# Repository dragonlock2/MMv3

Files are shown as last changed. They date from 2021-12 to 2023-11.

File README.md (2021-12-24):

# MMv3

MMv3 is the 3rd generation robot platform used to teach the IEEE Micromouse DeCal at UC Berkeley. It was designed with usability, manufacturability, size, and cost in mind.

## Setup

1. Follow the assembly instructions in [lab1](docs/lab1.md) using the latest **BOM** (see releases).
2. Plug mouse into your computer and upload the latest **firmware.uf2** (see releases) by dragging the file into the `RPI-RP2` folder that shows up. It should disappear and reappear as a `CIRCUITPY` folder.
    * If you've uploaded firmware before, you'll need to hold the `BOOTSEL` button on the Pi Pico while plugging in.
3. Download the latest CircuitPython [libraries](https://circuitpython.org/libraries) (for Version 7.x) and upload the following ones to the lib/ folder on your mouse.
    * adafruit_motor/
    * adafruit_onewire/
    * neopixel.mpy

## Labs

Skeleton lab code, lab documents, and solutions are stored in [labs/](labs/), [docs/](docs/), and [solutions/](solutions/), respectively. To get started with a lab, simply copy the contents of the folder over to the CircuitPython drive and edit files from there.

* [sanity](docs/sanity.md) - Hardware Check
* [lab1](docs/lab1.md) - Assembly and CircuitPython Basics
* [lab2](docs/lab2.md) - Encoders
* [lab3](docs/lab3.md) - IR Sensors
* [lab4](docs/lab4.md) - Odometry and Motor Control
* [lab5](docs/lab5.md) - Intro to PID
* [lab6](docs/lab6.md) - More PID
* [lab7](docs/lab7.md) - Maze Solving Primitives **(WIP)**
* lab8 - Flood Fill **(WIP)**

## Compiling CircuitPython

The DS28E05 1-Wire EEPROM operates at overdrive speeds only. Adding support involves compiling a patched version of CircuitPython.

1. Follow these [instructions](https://learn.adafruit.com/building-circuitpython/introduction) to get your system set up for compilation.
2. Follow these [instructions](https://learn.adafruit.com/building-circuitpython/build-circuitpython) to clone CircuitPython and do further setup but don't compile CircuitPython just yet.
3. Apply [circuitpython.patch](circuitpython.patch) using `patch -p1 < circuitpython.patch`
    * Also apply [macos.patch](macos.patch) if using MacOS.
4. Compile CircuitPython with `cd ports/raspberrypi && make  BOARD=raspberry_pi_pico`
5. Upload the resulting firmware.uf2!

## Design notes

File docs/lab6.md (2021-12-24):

# Lab 6: More PID

## Background

In the previous lab we were able to get our mice driving a certain distance reasonably straight with just proportional control. This week, we'll learn how to correct for persistent steady state error, turn in place, and follow walls.

Recall our implementation of a **proportional (P) controller** from the last lab.

<p align="center">
    
</p>

Proportional control works pretty well for making our mouse drive straight, but you may have noticed a constant offset error. The motors naturally travel at different speeds given the same power and the constant offset error actually accounts for that difference. If we had zero error, we'd actually apply the same power to each motor, generating an error. How might we fix this? What if we kept track of the total error?

<p align="center">
    
</p>

This is called a **proportional-integral (PI) controller**. The integral keeps track of the total error (both positive and negative) since we first started the controller. Even small errors will cause the integral term to eventually grow large enough and get  to push our mouse back on track.

In order to dampen oscillations and prevent overshoot, we might want to consider the derivative of our error too. This prevents our error from changing too quickly.

<p align="center">
    
</p>

With these three terms, we have our **proportional-integral-derivative (PID) controller**. , , and  are tunable gains that determine the behavior of our error (rise time, peak, overshoot, etc.).

Let's go over what each of the terms in PID means.

* The **P** term (**proportional**) increases our correction proportionally to the error: the higher our error, the more power we should apply to correct for it.
* The **I** term (**integral**) compensates for long-term error and drift by integrating the error over time. While a small tendency for our mouse to veer to the right might have little effect on the P term, it’ll cause the I term to build up until the system reaches the setpoint perfectly.
* The **D** term (**derivative**) takes the derivative of the error with respect to time. Systems often have inertia: the faster our error is already decreasing, the less power we need to apply to correct for it. This dampens our controller and reduces overshooting.

Note this checkpoint has no code.

### Checkoff #1

1. We only have individual measurements of error, not a continuous function. How might we estimate the integral of the error?
2. How might we estimate the derivative of the error?
3. One potential issue with PID control is **integral windup**. You can read about it [here](https://en.wikipedia.org/wiki/Integral_windup). What are some ways of preventing integral windup?

## Turning

Copy over the skeleton code in [labs/lab6/](../labs/lab6) onto your mouse. To encourage code readability, we've added a couple of function definitions that modularize the controller. Adapt your P controller code from [Lab 5](lab5.md) to these functions by filling out the TODOs. If you have a better way of organizing the functions, feel free to change things. Ultimately, it should have the same behavior as Checkoff #2 from Lab 5.

Next, add I and D terms to both your angular and linear P controllers. You may find the `global` or `nonlocal` keywords to be useful for accessing variables defined outside of a function. We highly recommend just tuning the PID constants for your linear controller first and then tuning the angular controller when you implement turning. It's generally easier when that specific controller is being exercised. Good starting values are 10x smaller than .

Finally, have your mouse turn 90° in place. This should be as simple as setting a different target . For an added challenge, let's create a `turn_left` function which internally loops until the mouse turns about 90° (you choose the threshold for acceptable error) before returning. You may find it useful to be able to reset the odometry back to 0 with the following function.

```python
def reset_odometry():
    lenc.position, renc.position = 0, 0
```

### Checkoff #2

1. Demonstrate your working PID loop driving straight a set distance.
2. Demonstrate your working PID loop turning in place by 90°.
3. Demonstrate turning in place by 90° and then stopping for one second before turning another 90° and so on.
4. Explain your implementation of your integral term. Did you account for integral windup?

## Wall Following

When we're driving in a maze, our mouse will always be slightly misaligned with reference to a wall. Despite driving perfectly straight, this slight error will eventually cause us to crash. By performing feedback control with our IR sensors, we can correct for any misalignment!

In the interest of developing maze solving primitives in the future, you will implement a `forward()` function that will have the mouse drive forwards 180mm and stop. While driving forward, maintain a fixed 45mm distance from a wall on the left.

Optimally, stable wall following means maintaining a 0° angle with respect to the wall. With just one sensor, it's impossible to determine the angle because multiple angles can correspond to the same sensed distance. Performing feedback control on just that sensor works, but it relies on the mouse moving a bit to correct for angular errors. With two sensors, we can determine the angle from the wall based on the difference between the sensors. Wall following could then be implemented as just setting the angle of the mouse based on the distance error and letting its forward motion correct for the distance error.

To implement wall following, start by taking your distance measurement code from lab 3 and your linear and angular PID controllers from the previous checkoff. Conceptually, we want to change the definitions of `theta` and `theta_target` for the angular controller. Based on what was discussed previously, what are the new definitions of `theta` and `theta_target`?

Don't worry about implementing a PID controller for this as a P controller is adequate. Tuning can be a bit tricky. We've found that `Kp_theta=0.01` and `Kp_ang=0.01` work pretty well. Our reference solution uses `Kp_theta` to scale the distance error to set `theta_target`. Since we assume the mouse drives pretty straight and isn't very misaligned, don't worry about tuning your controller to work well for large errors.

### Checkoff #3

1. Demonstrate your wall following code by calling `forward()` once every second.
2. How might you extend your code to drive straight in between two walls?

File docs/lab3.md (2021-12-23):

# Lab 3: IR Sensors

## Background

IR sensors work by sending out IR light and measuring the amount reflected back. They take a lot more work to calibrate and are surface dependent, but are far cheaper and faster than the ToF sensors we used to use. Our mouse has 6 of these sensors split into 3 pairs (center/front, left, right). Having 2 sensors per side allows us to statically determine both the distance and angle of the nearest surface.

IR sensors consist of both an IR emitter and detector. IR emitters draw around 50mA each when on, so we have a switch to turn them off when not needed. IR detectors shift their IV curve based on light intensity like in the following graph.

<p align="center">
    
</p>

To convert that to a readable voltage signal, we'll use a setup similar to a resistor divider. It's noisier and less tunable compared to a transimpedance amplifier, but uses only one resistor. By placing the IR detector in reverse bias, we use the flatter region of the IV curve. Since the current varies linearly with light intensity, the voltage also varies linearly. MMv3 uses the following circuit (pull-up resistor not shown).

<p align="center">
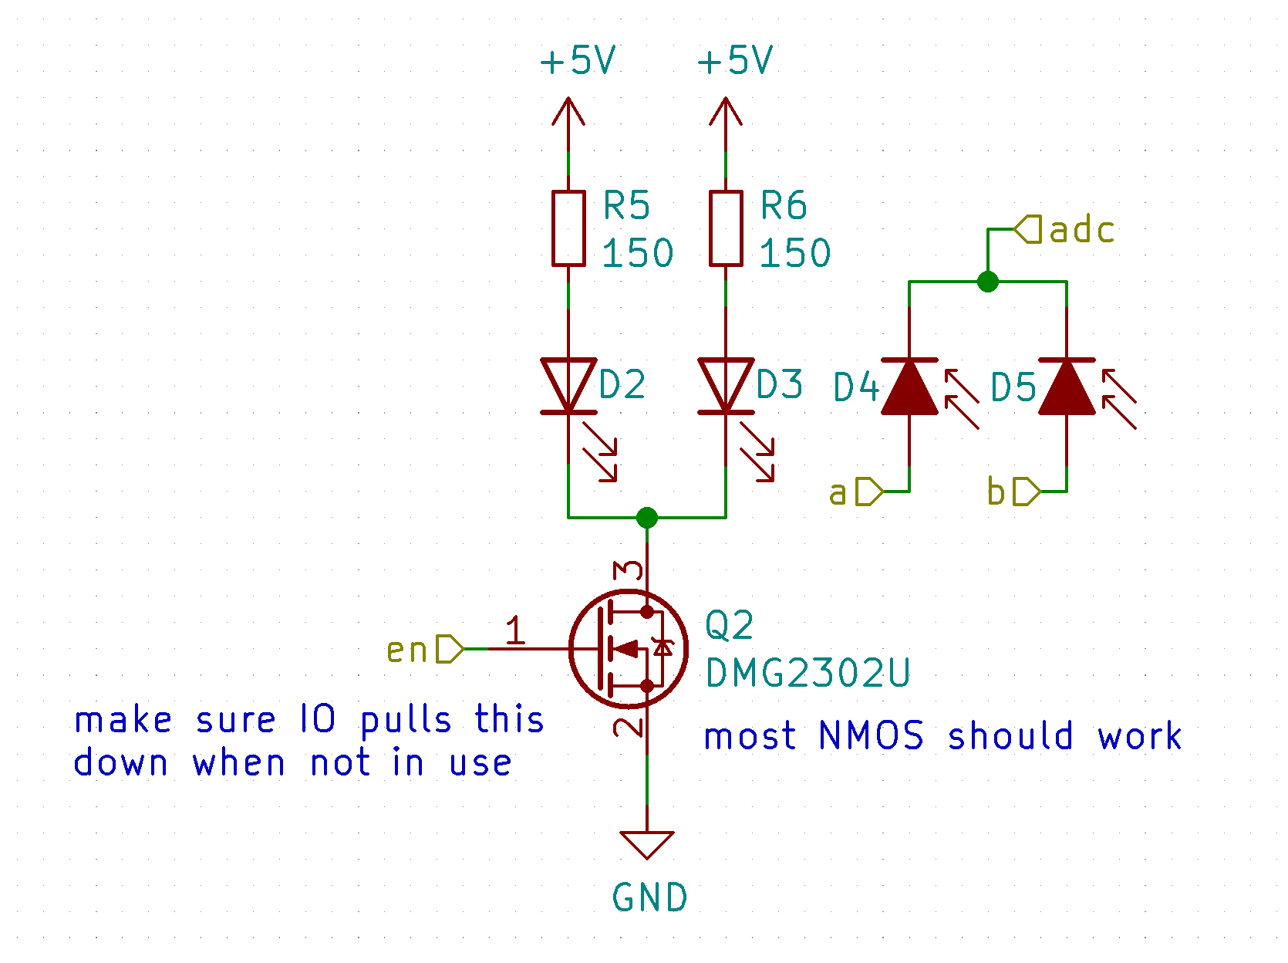
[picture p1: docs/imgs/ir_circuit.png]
    
</p>

## Read One Sensor

Since we have 6 total analog sensors but only 3 ADC pins on the Pi Pico, we need to multiplex 2 sensors onto each pin. We use one extra pin on each IR detector in open-drain mode to fully disconnect or connect it to ground. To read in one sensor, we perform the following steps.

1. Enable the IR emitters (set pin to `True`).
2. Enable the chosen sensor by connecting it to ground (set pin to `False`).
3. Wait around 1ms for things to settle.
4. Take the reading.
5. Disable the chosen sensor by setting the pin to open-drain (set pin to `True`).
6. Disable the IR emitters (set pin to `False`).

Baesd on the above steps and the `AnalogIn` [documentation](https://circuitpython.readthedocs.io/en/latest/shared-bindings/analogio/index.html), fill out the below TODOs to print out readings from the left IR sensor pair (`lir_a` and `lir_b`).

```python
import board
import time
import digitalio
from analogio import AnalogIn

l_en  = """TODO create DigitalInOut output on GP7"""
l_adc = """TODO create AnalogIn on GP28"""

l_a   = digitalio.DigitalInOut(board.GP5)
l_a.direction  = digitalio.Direction.OUTPUT
l_a.drive_mode = digitalio.DriveMode.OPEN_DRAIN
l_a.value = True # high Z mode

l_b = """TODO create DigitalInOut on GP6 in open-drain mode"""

while True:
    # TODO enable IR emitters using l_en
    # TODO enable chosen sensor l_a or l_b
    # TODO wait a bit
    # TODO take analog reading for future printing
    # TODO disable chosen sensor l_a or l_b
    # TODO disable IR emitters using l_en
    time.sleep(0.05)
```

### Checkoff #1

1. Demonstrate one working sensor.

## Read All the Sensors

In order to simplify the whole process of multiplexing and reading from multiple sensors, we wrote a library. Upload `irsensor.py` from [sanity/](../labs/sanity) to serve as the library. Read through `irsensor.py` to instantiate and use it and fill out the below TODOs to print out all sensor readings in real time.

```python
import board
import time

from irsensor import IRSensors

ir = IRSensors(
    """TODO sensor | en   | a    | b    | adc"""
    """TODO lir    | GP7  | GP5  | GP6  | GP28"""
    """TODO cir    | GP9  | GP10 | GP11 | GP26"""
    """TODO rir    | GP21 | GP20 | GP22 | GP27"""
)

while True:
    """TODO get and print all sensor readings"""
    time.sleep(0.05)
```

### Checkoff #2

1. Demonstrate all of your working sensors.

## Calibration

Let's try estimating actual distances from the sensor values. Empirically, the relationship is linear below around 60mm and rises sharply beyond that due to the angled sensors seeing above the wall. Based on maze cell size, we really only need accurate distances around 50mm for wall following and just binary wall detection beyond that.

<p align="center">
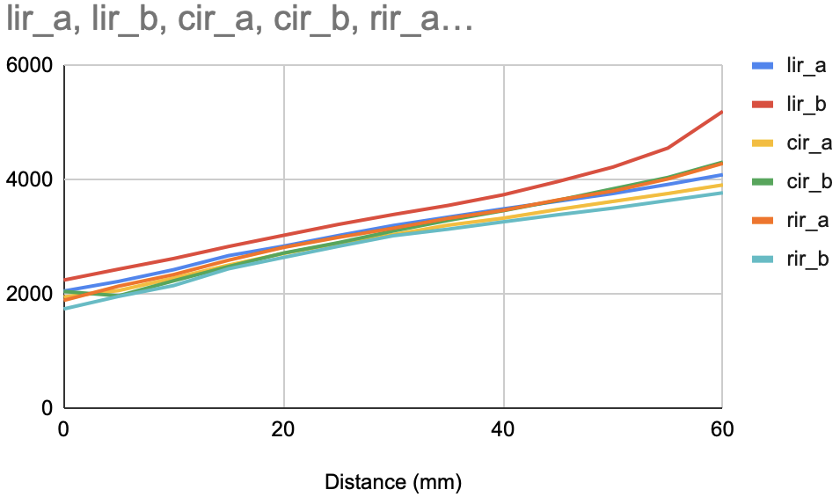
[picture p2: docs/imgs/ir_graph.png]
    
    <br>
    <a><b>IR Sensor Linear Region</b></a>
</p>

Load up [`code.py`](../labs/lab3/code.py) which contains code to automate finding the constants. You'll be using a maze wall and ruler to take readings at various distances. The code then uses least squares to fit a line to the points and prints out the constants at the end. The equation using these constants to convert sensor readings to distances can be expressed as follows.

<p align="center">
    
</p>

### Checkoff #3

1. Run the calibration code and save the constants somewhere.
2. Using the constants, write code to convert sensor values to distances.

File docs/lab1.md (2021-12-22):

# Lab 1: Assembly and CircuitPython Basics

## Assembly

Download the `ibom.html` from the [release](https://github.com/dragonlock2/MMv3/releases) that matches your board revision and open it in your preferred browser. The interactive BOM (bill of materials) shows what parts are needed on your mouse's PCB (printed circuit board) and where they need to be placed.

Also check the latest release for any manufacturing notes to make an older board functionally equivalent to the newest revision.

### Reflow Soldering

Let's start with the back of the PCB which is where the majority of parts are located. Click `B` in the top right to show just the back.

<p align="center">
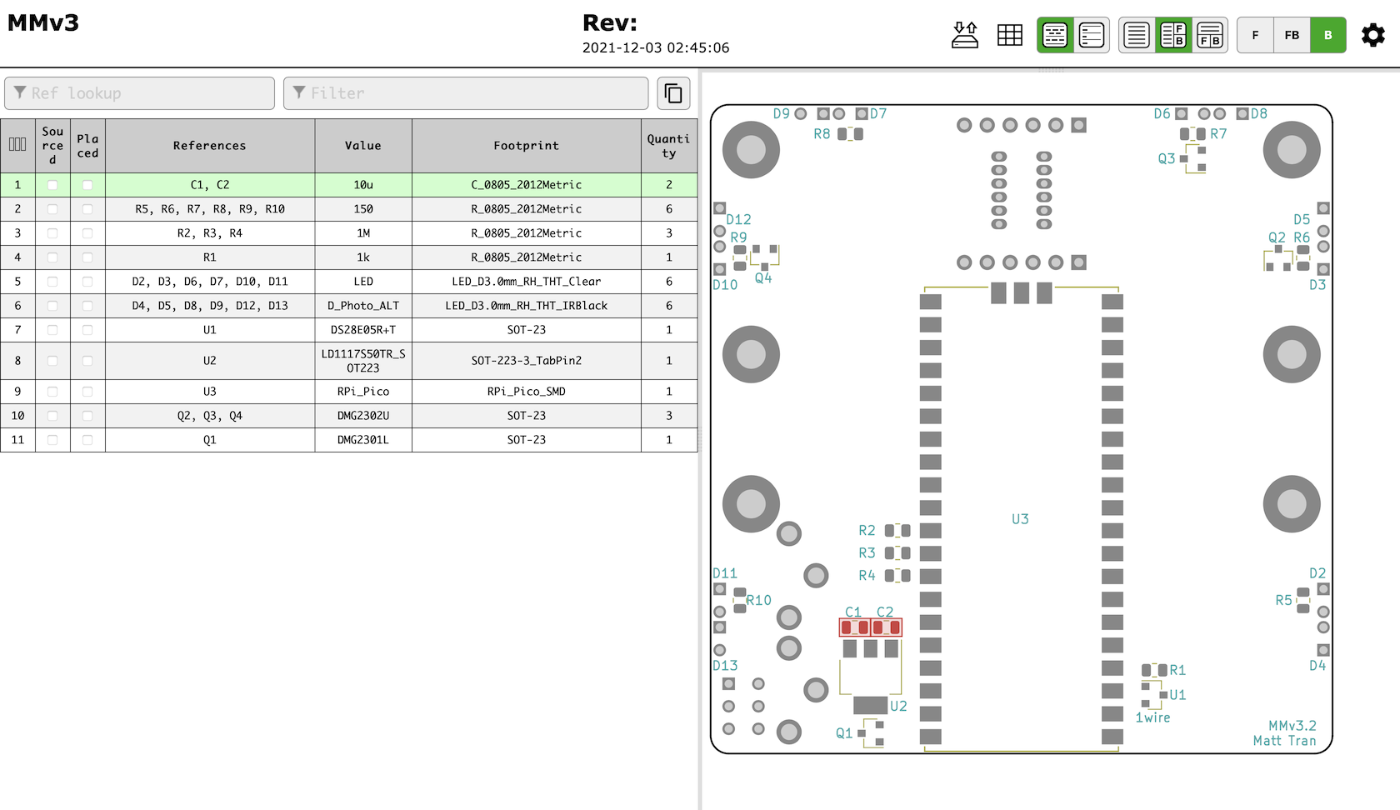
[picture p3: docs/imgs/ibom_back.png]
    
    <br>
    <a><b>iBOM Back</b></a>
</p>

Rather than solder each part by hand, we'll use reflow soldering which does it all at once. In reflow soldering, we place components on top of pads covered in solder paste before sending the whole thing through an oven to melt the solder, making permanent joints.

<p align="center">
    
    <br>
    <a><b>Reflow Solder Process</b></a>
</p>

Let's start by applying the solder paste using a **solder stencil**. Instead of squeezing the perfect amount onto each pad by hand, we can do it all at once by spreading paste over a stencil with holes cut out precisely where we want paste. For a good solder paste application, it's important to make sure the stencil is flush against the PCB and stays aligned. The process is very forgiving, so don't worry if your paste looks messy or goes a bit outside the pads.

<p align="center">
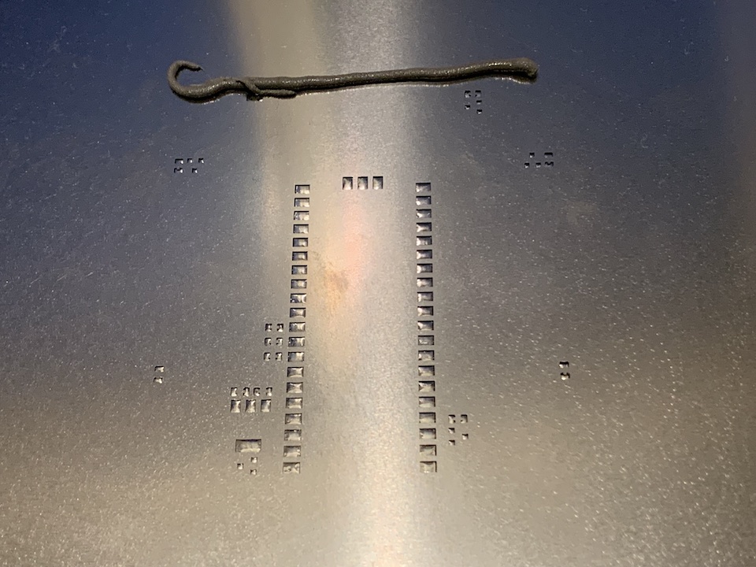
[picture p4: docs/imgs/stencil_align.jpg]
    
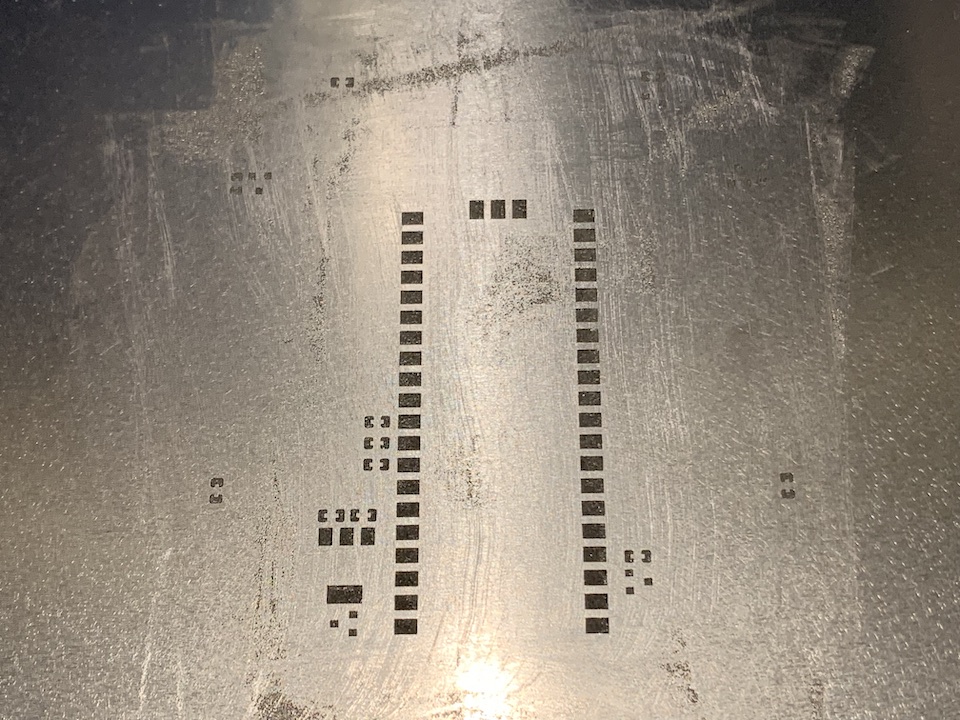
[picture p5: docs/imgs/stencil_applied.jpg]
    
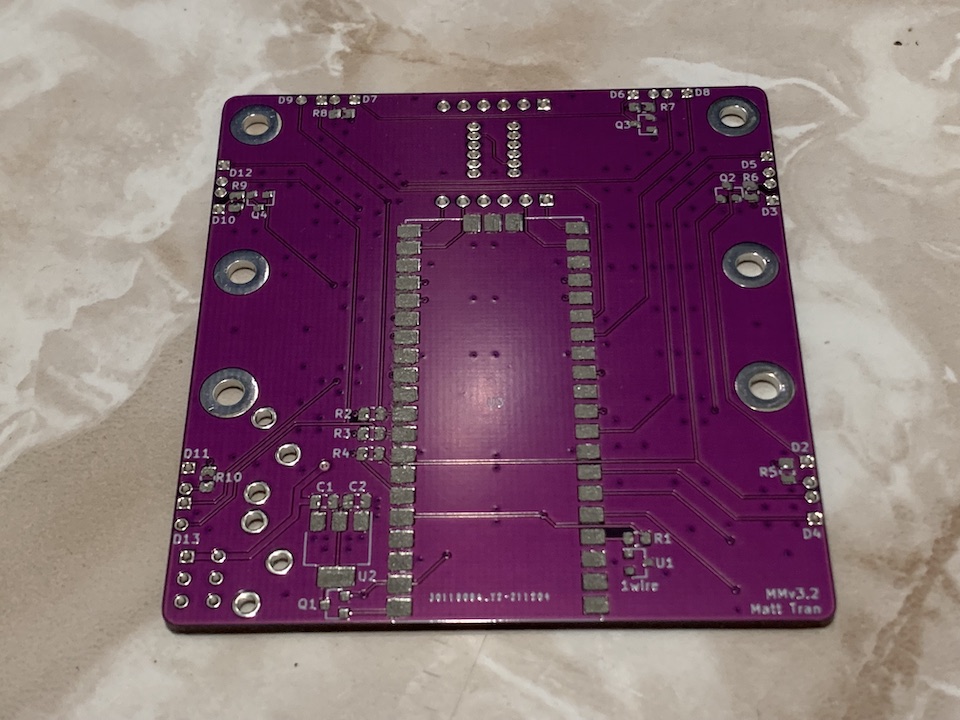
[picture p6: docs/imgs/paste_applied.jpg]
    
    <br>
    <a><b>Solder Paste Application Process</b></a>
</p>

Now it's time for component placement. Following the `ibom.html`, place all of the components for the back side. None of the symmetric components have polarity, so don't worry about part orientation. Tweezers will be very useful, but don't squeeze too hard or your component will go flying. When placing components, press down gently so that it digs into the paste a bit to prevent it from moving. Again, the process is quite forgiving so don't worry if your parts aren't perfectly aligned as solder surface tension will generally pull them into alignment.

<p align="center">
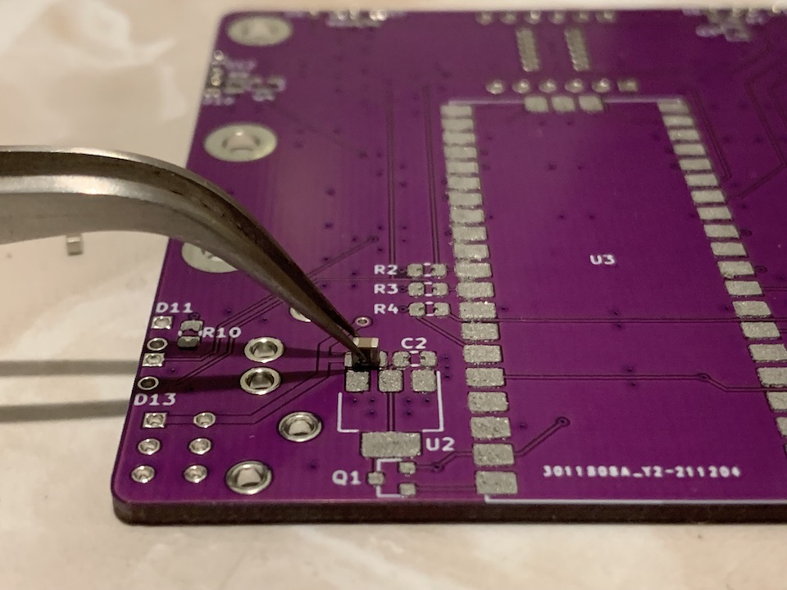
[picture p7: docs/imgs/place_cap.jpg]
    
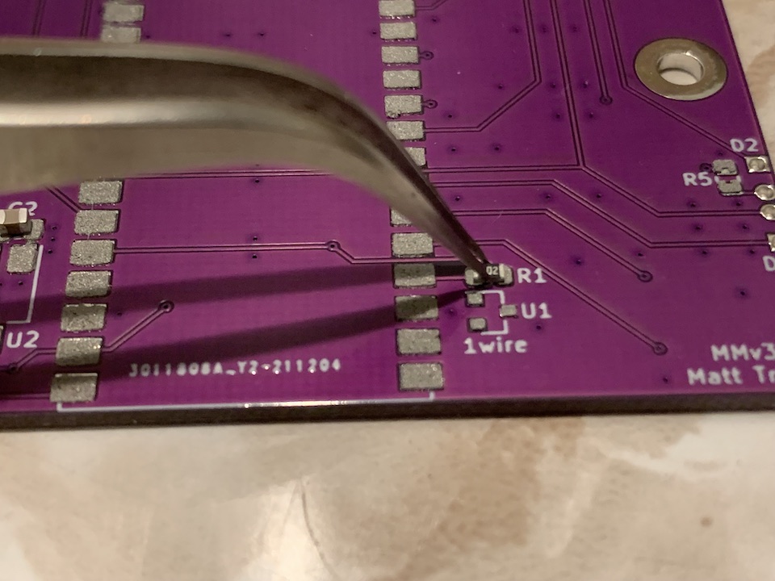
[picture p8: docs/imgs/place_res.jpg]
    
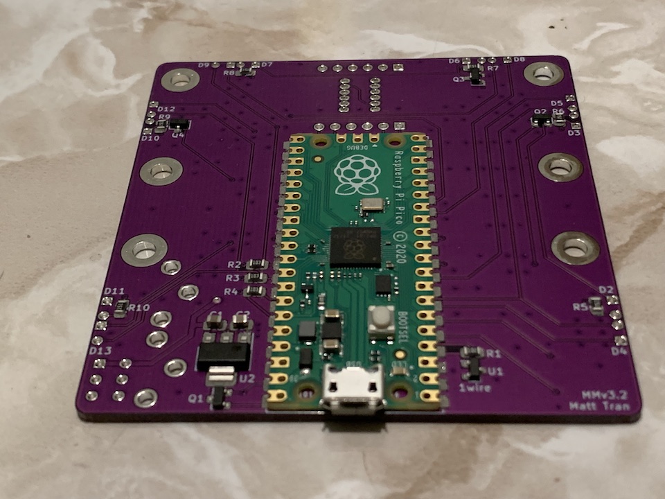
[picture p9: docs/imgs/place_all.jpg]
    
    <br>
    <a><b>Component Placement</b></a>
</p>

Finally, let's reflow the solder! Throw your board into the reflow oven, load up the correct profile, and wait. With any luck, all of your joints will melt and the back side of your board will be done.

<p align="center">
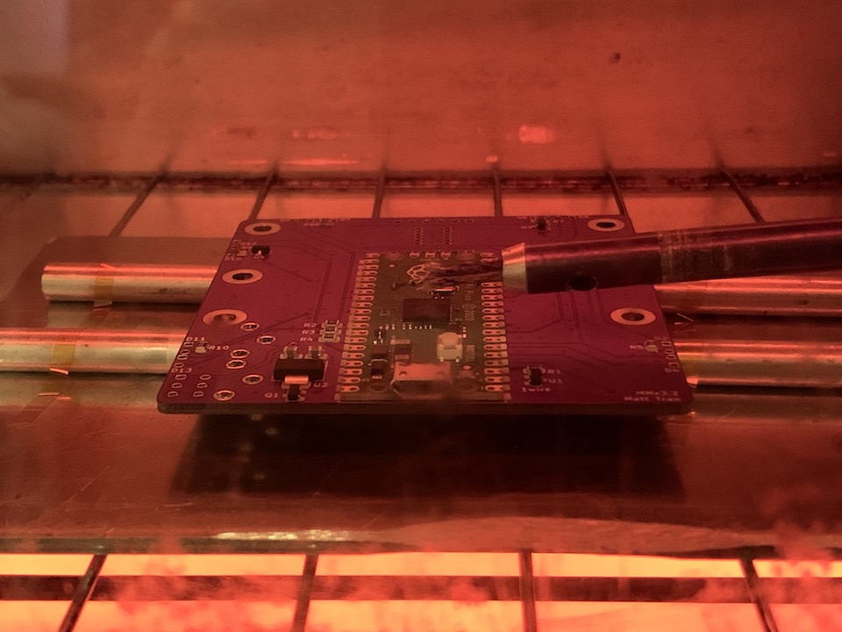
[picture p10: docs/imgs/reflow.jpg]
    
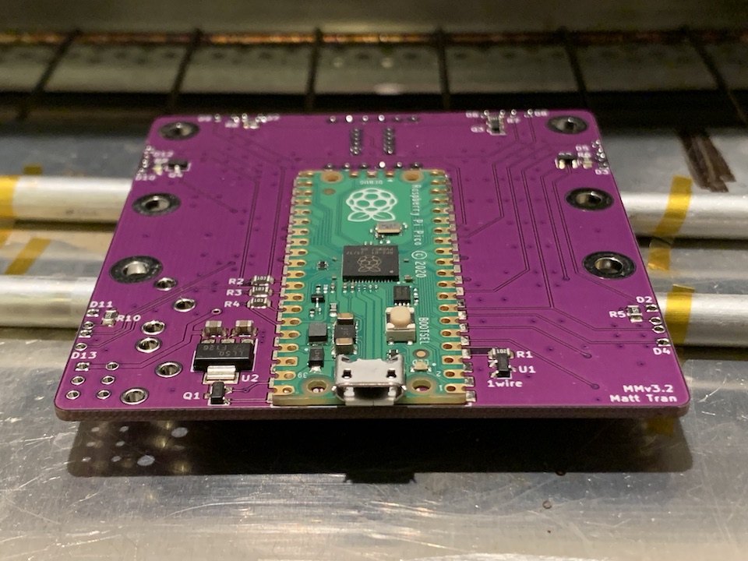
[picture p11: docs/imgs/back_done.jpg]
    
    <br>
    <a><b>Reflow</b></a>
</p>

### Hand Soldering

The rest of the components need to be attached by hand. The general process is to heat up both the pad and the part before melting solder onto both of them. Adafruit has a great list of common issues and fixes which can be found [here](https://learn.adafruit.com/adafruit-guide-excellent-soldering/common-problems).  

<p align="center">
    
    <br>
    <a><b>How to Make a Solder Joint</b></a>
</p>

Let's start with the DRV8833 motor driver board. Solder the two 6-pin headers onto the board and bridge the `en` pads as shown in the following pictures. The technique that I find works best is to solder just one pin first with the part in any orientation. Then reheat that joint while pressing on the part to move it into perfect alignment. Finally, do the rest of the pins.

<p align="center">
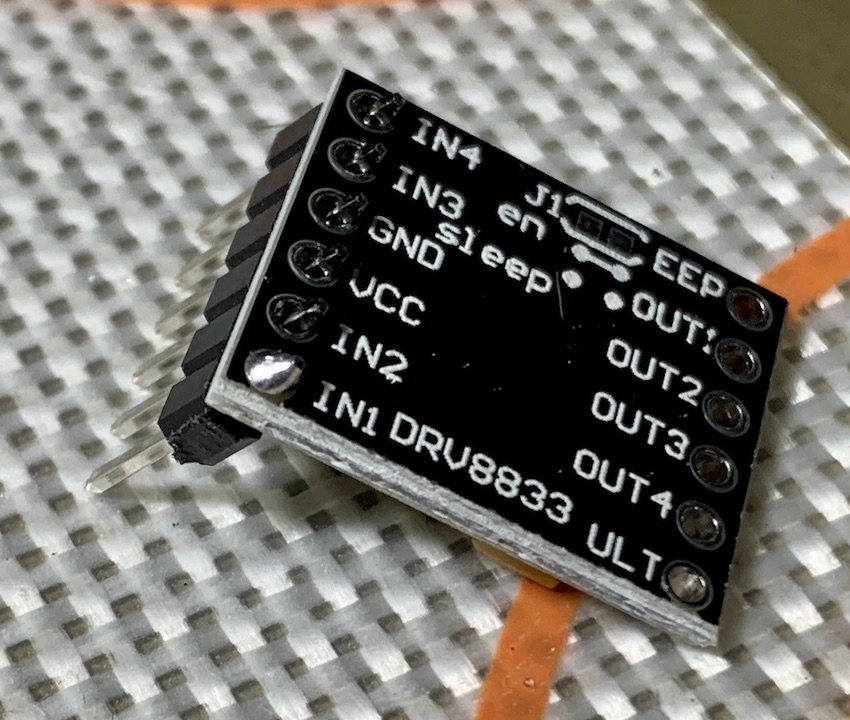
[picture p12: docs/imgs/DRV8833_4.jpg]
    
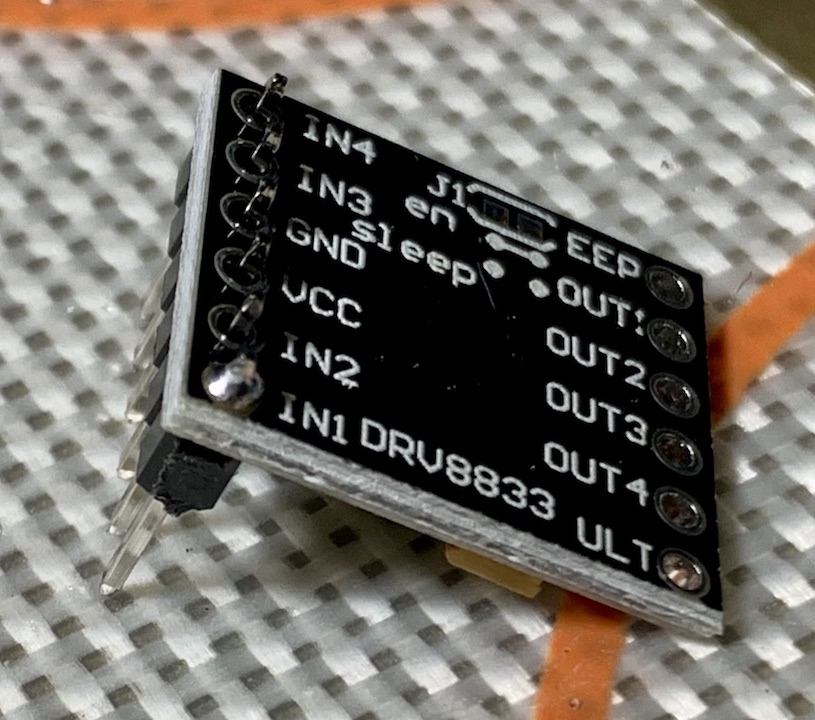
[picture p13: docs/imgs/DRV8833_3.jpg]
    
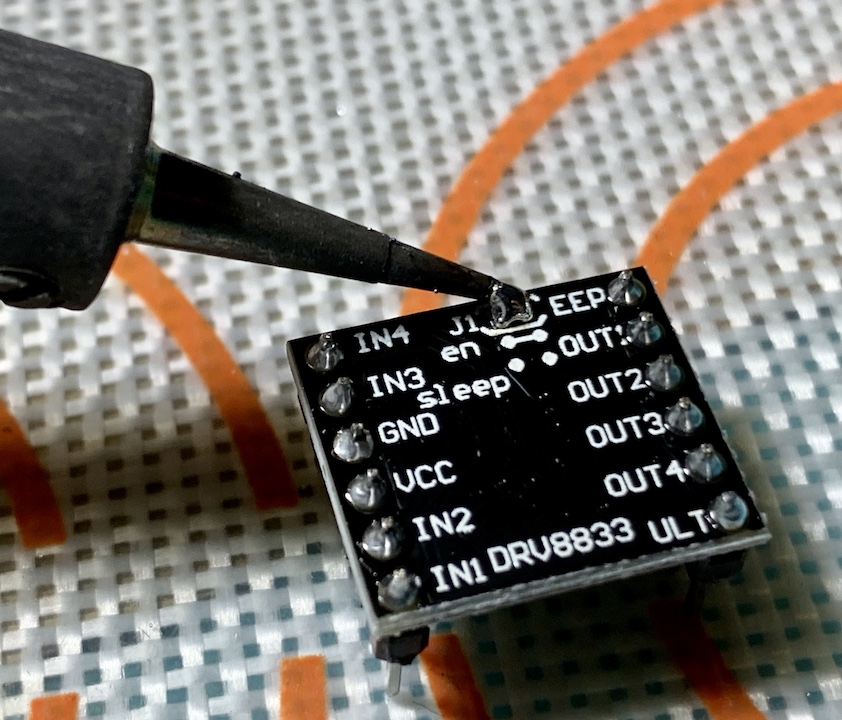
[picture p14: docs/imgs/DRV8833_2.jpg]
    
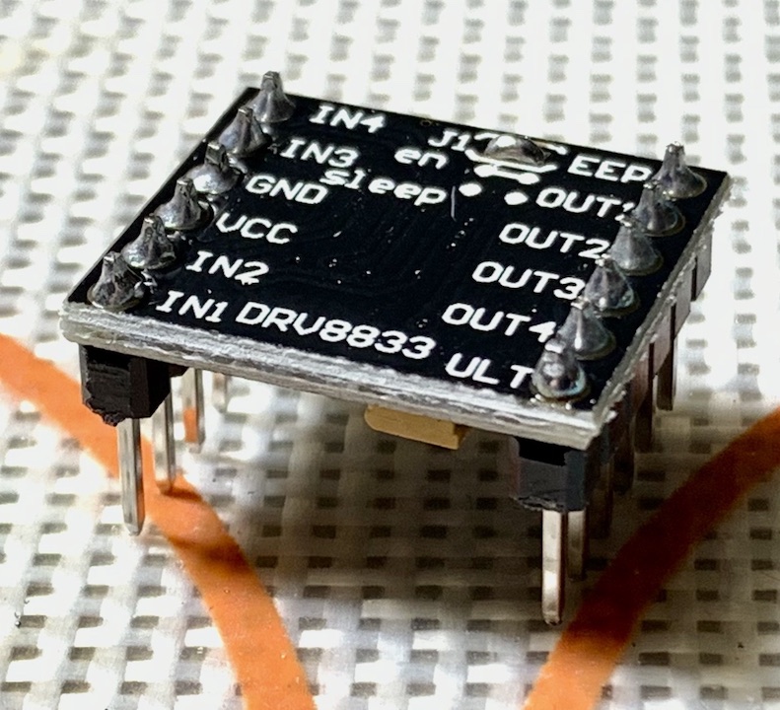
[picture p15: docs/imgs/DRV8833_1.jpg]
    
    <br>
    <a><b>DRV8833 Motor Driver Assembly</b></a>
</p>

Next let's finish off the mouse's main PCB. Click `F` in the `ibom.html` to see the remaining components.

<p align="center">
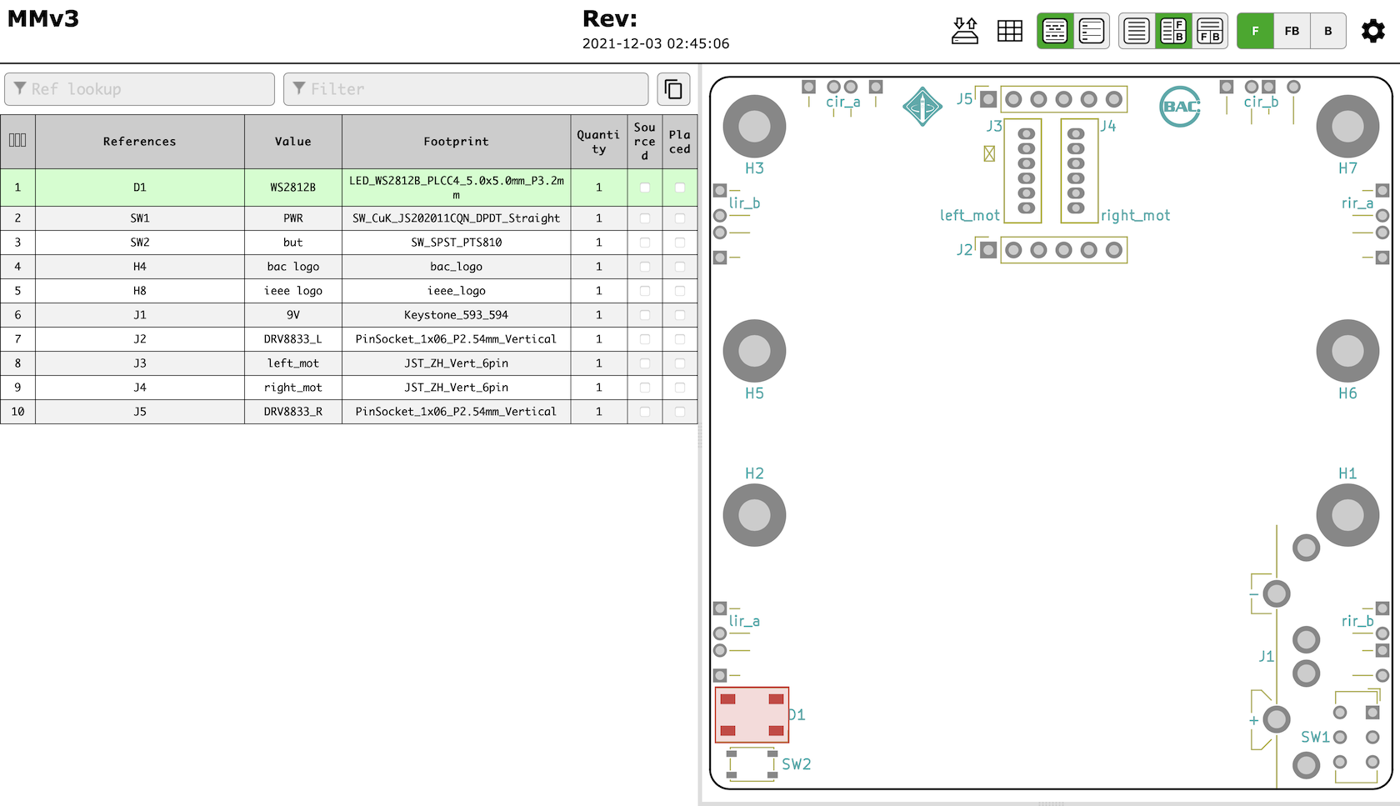
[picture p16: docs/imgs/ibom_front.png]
    
    <br>
    <a><b>iBOM Front</b></a>
</p>

To make alignment easier, starting with the shortest components usually works out best. The SMD components use the same soldering process except there's no hole to stick the part through. Some of the parts do have polarity, so if you're unsure make sure to ask your mentor.

<p align="center">
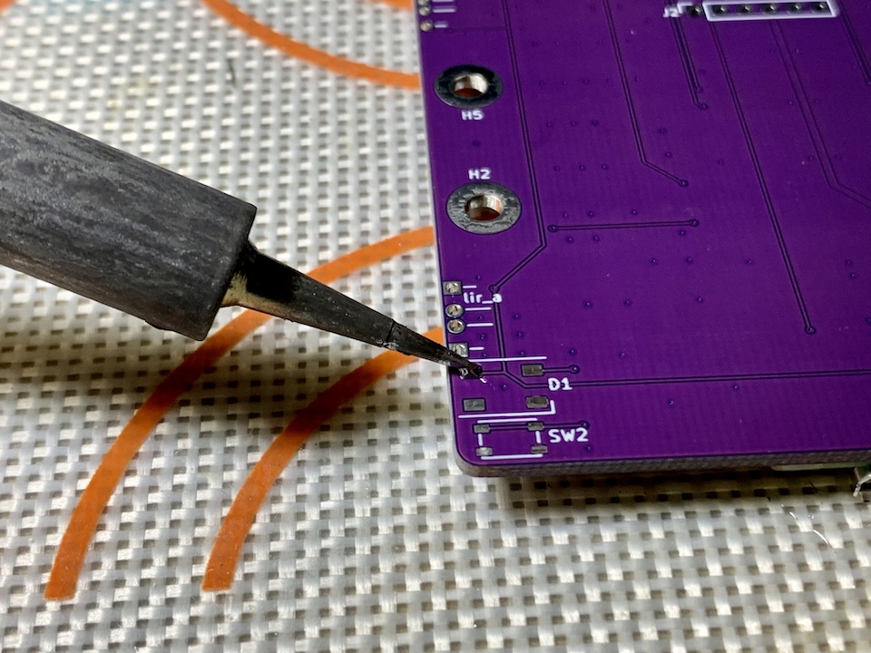
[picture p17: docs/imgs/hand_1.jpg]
    
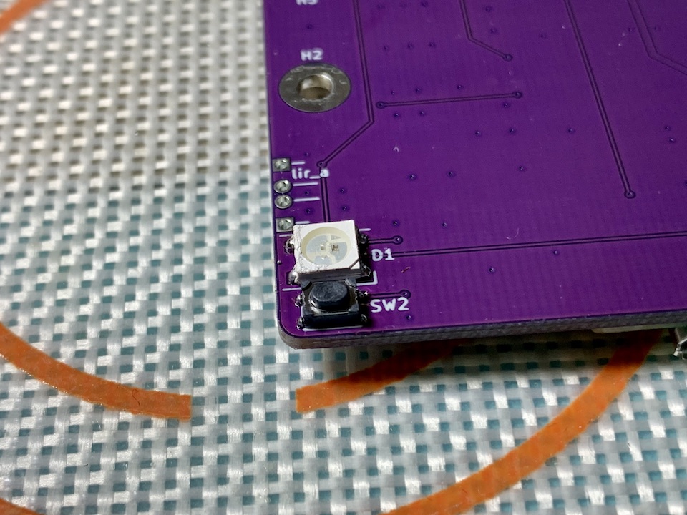
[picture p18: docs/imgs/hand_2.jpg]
    
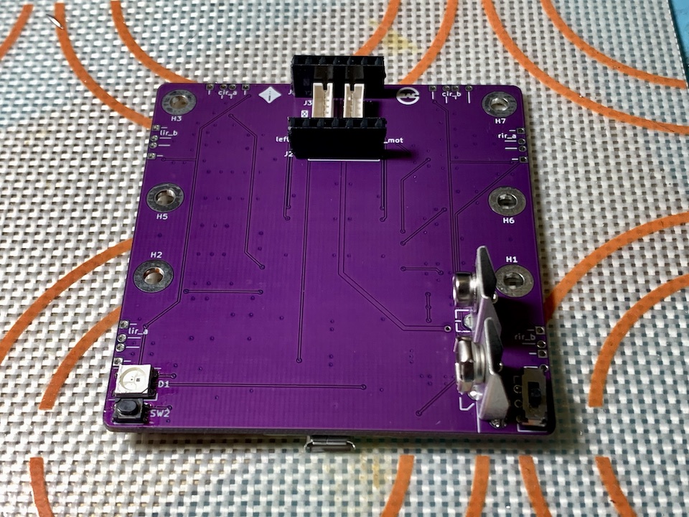
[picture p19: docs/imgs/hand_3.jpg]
    
    <br>
    <a><b>Some THT Components</b></a>
</p>

For the IR LEDs, the silkscreen should denote the polarity. They also need to be mounted at a right angle so don't be afraid to bend them. Splaying the leads outward should hold them in place while you apply solder.

<p align="center">
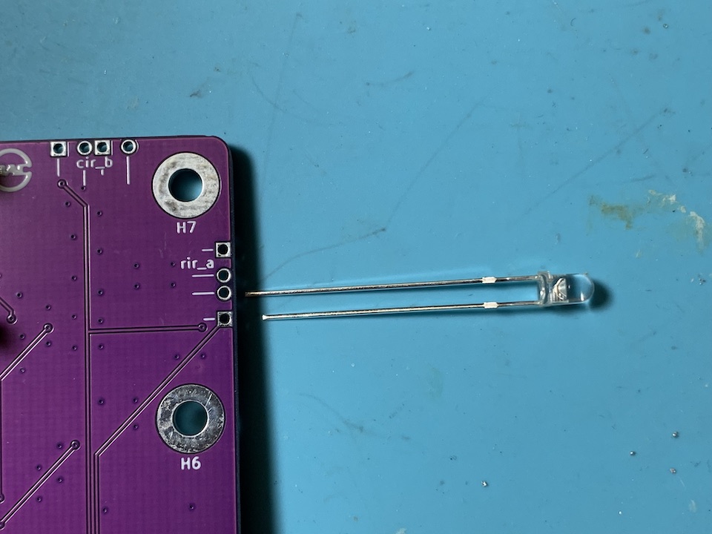
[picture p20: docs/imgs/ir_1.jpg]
    
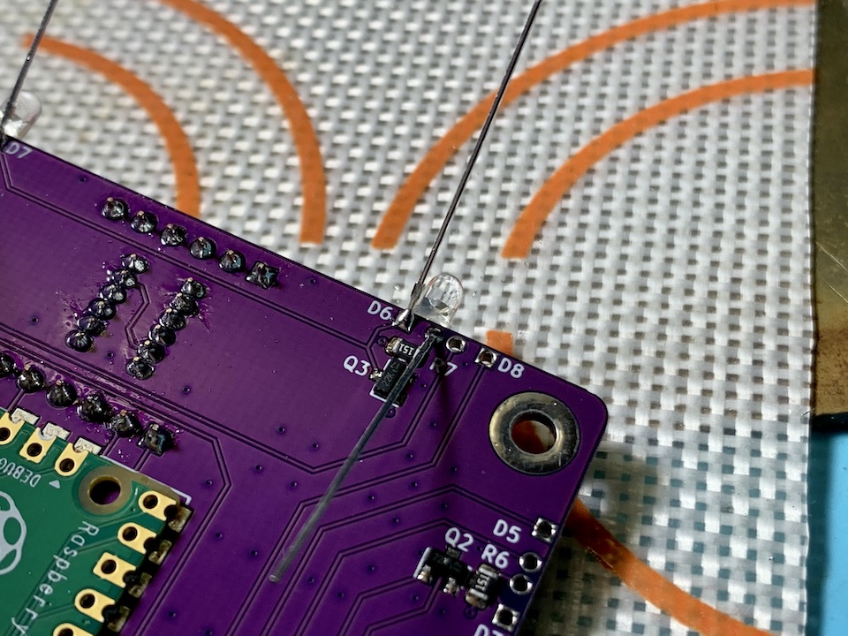
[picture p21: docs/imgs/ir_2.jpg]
    
    <br>
    <a><b>IR LEDs</b></a>
</p>

With any luck, your board should be finished!

<p align="center">
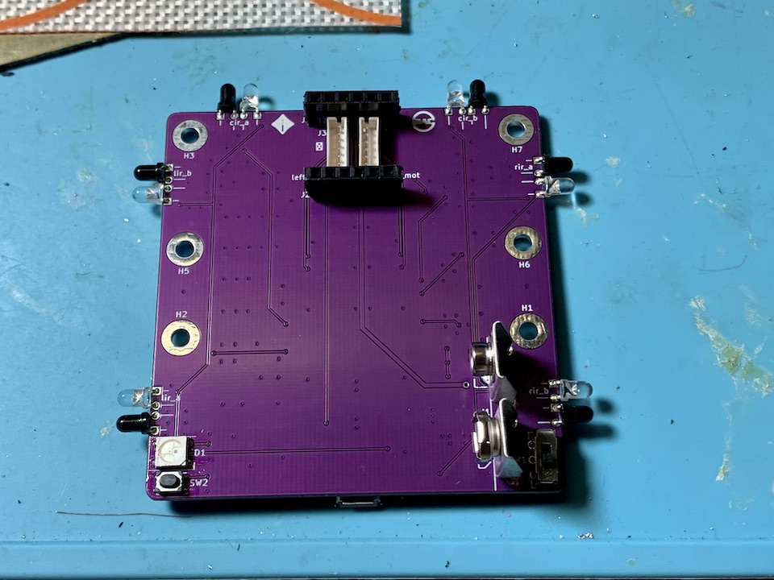
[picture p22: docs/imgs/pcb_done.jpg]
    
    <br>
    <a><b>Assembled PCB</b></a>
</p>

### Mechanical Assembly

Let's finish assembling the mouse. Follow the pictures below. The screw threads are printed into the plastic so don't overtighten them. Don't be afraid to apply a bit of force when attaching the wheels since a tighter fit improves concentricity.

<p align="center">
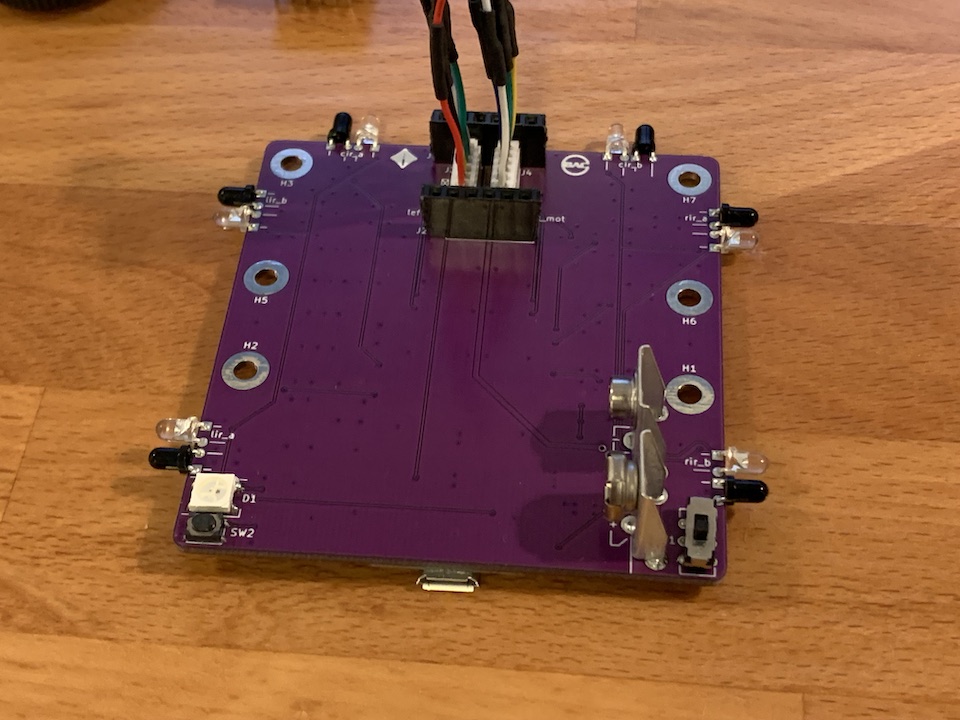
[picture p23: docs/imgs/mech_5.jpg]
    
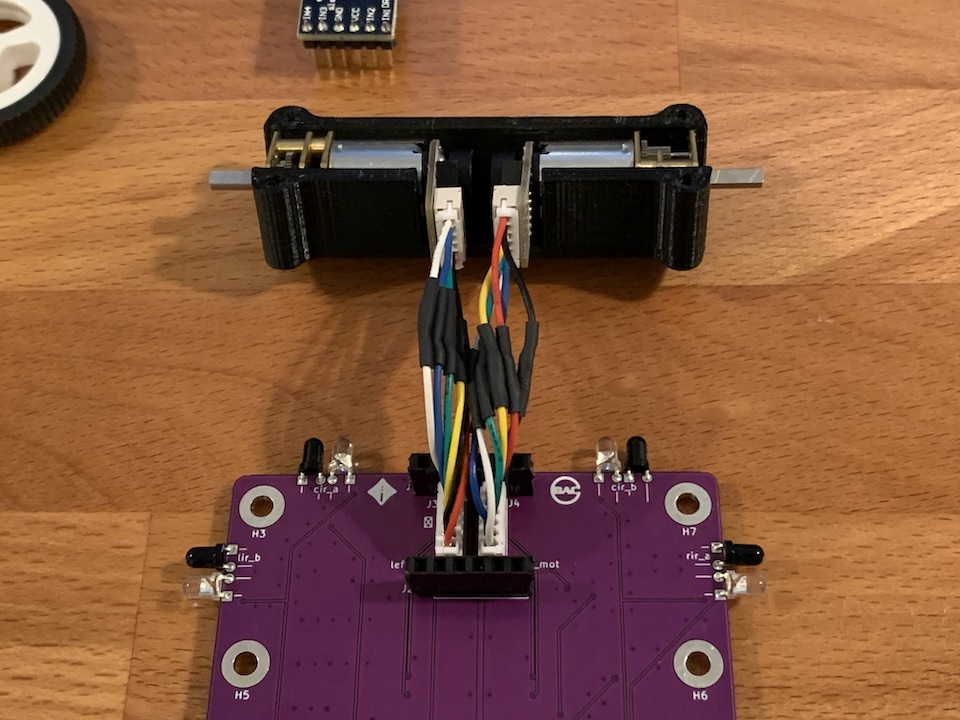
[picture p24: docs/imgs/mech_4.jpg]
    
    
    
    
    <br>
    <a><b>Final Assembly</b></a>
</p>

## Sanity Check

Now that your mouse is assembled, it is time to run a sanity check to make sure everything is working.

1. Follow the [setup](../README.md) instructions to get the firmware and libraries uploaded.
2. Follow the [sanity lab](sanity.md) to run the sanity check.

## IR Calibration

If you placed your mouse against a reflective surface, you may have noticed that the IR readings change. Since our sensors are currently mounted perpendicular to the mouse, they pick up some reflection from the surface the mouse sits on. To fix this, we're going to bend our IR sensors ever so slightly upwards to compensate.

Bring up the sanity check again to the IR sensor printout section. Bend your IR sensors upwards just enough so that the difference between pointing them into free space and placing them on a surface is less than 2,000.

<p align="center">
    
    <br>
    <a><b>Bent IR Sensors</b></a>
</p>

### Checkoff #1

1. Show your mentor your assembled mouse, passing sanity check, and calibrated IR sensors.

## CircuitPython Basics

One of the most convenient features of CircuitPython is the ability to upload and modify code as if they were just files on a flash drive. Instead of editing code directly on the drive, we highly recommend **editing code locally** on your computer first and then copying it over to the drive to run. This reduces wear on the flash memory and ensures you have a local backup of your code.

On startup, CircuitPython looks for a file named `code.py` and runs it. There are a few differences, but for the most part it behaves just like normal Python. After uploading new code, you might need to bring up a serial monitor and press CTRL-C and CTRL-D to reload.

For debugging, the serial monitor is invaluable. This is where the output of `print` statements will go. You can even bring up a REPL. One important note is that you can't start an interactive session (e.g. `python -i code.py`) to further debug your code as CircuitPython will restart on entering one.

### Example 1: Blinky

Let's start with the blink example, the "Hello World" of embedded programming. Your mouse has a green LED on the Pi Pico and an onboard WS2812B NeoPixel RGB LED. Upload the following code to your mouse.

```python
import board     # pin definitions
import time      # time delay
import neopixel  # to control the WS2812B
import digitalio # to control the LED

print("Hello World!")

# setup the LED as an output
led = digitalio.DigitalInOut(board.LED)
led.direction = digitalio.Direction.OUTPUT

# setup the WS2812B
rgb = neopixel.NeoPixel(board.GP4, 1)

# blink
while True:
    rgb[0] = (255, 255, 255) # max brightness
    led.value = True
    time.sleep(0.5)
    rgb[0] = (0, 0, 0)
    led.value = False
    time.sleep(0.5)
```

Running the code, both LEDs should start blinking every 0.5s. Notice that before we start writing values to the LEDs, we need to set them up with the correct physical pin. Also, WS2812Bs can be chained into strings which is why we use `rgb[0]`, to address the first (and only) LED.

### Checkoff #2

1. Change something about the provided blink code such as RGB color and blink rate.

### Example 2: Unnecessarily Complex Blinky

Let's take a look at some more syntax. Upload the following code to your mouse.

```python
import board
import time
import neopixel

rgb = neopixel.NeoPixel(board.GP4, 1)

counter = 0
while True:
    counter += 1
    if counter % 5 == 0: # modulus a.k.a remainder
        rgb[0] = (100, 0, 0)
        time.sleep(0.5)
        rgb[0] = (0, 0, 0)
    else:
        for i in range(5): # 0, 1, 2, 3, 4
            time.sleep(0.1)
```

Here we introduce a couple programming constructs that are very common in coding. The `if` statement (pairable with `elif` and `else`) runs the block of code corresponding to the truthiness of what's next to the `if`. The `for` loop sequentially iterates through an object which in this case is `range(5)`.

### Checkoff #3

1. What is the blink pattern? How long is it on and off for?

### Example 3: 

Finally, let's test out the button on your mouse. It's connected to pin `GP3`. Fill in the TODOs below to have your RGB LED change color when the button is pressed.

```python
import board
import time
import neopixel
import digitalio

rgb = neopixel.NeoPixel(board.GP4, 1)

but = digitalio.DigitalInOut("""TODO which pin?""")
but.pull = digitalio.Pull.UP

while True:
    if but.value: # not pressed
        """TODO one color"""
    else: # pressed
        """TODO other color"""
```

### Checkoff #4

1. Demonstrate your working code.

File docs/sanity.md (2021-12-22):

# Sanity

This lab provides code to test all aspects of your mouse and identify any hardware defects. If at any point in this lab a test is not passed, ask an instructor for help debugging.

1. Upload the contents of [sanity/](../labs/sanity/) to the CircuitPython drive that shows up when you plug your mouse into your computer.
2. Find the associated serial port for your mouse.
    <details>
    <summary>Windows</summary>

    Open up `Device Manager` and check the `Ports (COM & LPT)` dropdown. Your serial (COM) port is one of those. If it's hard to identify, try unplugging and replugging your mouse and see which COM port disappears.

    </details>
    <details>
    <summary>MacOS</summary>

    Run `ls  /dev/tty.*` in Terminal. The correct port is one of those. If it's hard to identify, try unplugging and replugging your mouse and see which port disappears.

    </details>
    <details>
    <summary>Linux</summary>

    Hello there! A fellow power user you are. Your distro may be different, but chances are it's under something like `/dev/ttyACM0`.

    </details>
3. Bring up a serial monitor on that serial port (baud rate doesn't matter). There are many options of software to use, but the following are what I personally use.
    * **Windows** - [PuTTY](https://www.chiark.greenend.org.uk/~sgtatham/putty/latest.html)
    * **MacOS** - [SerialTools](https://apps.apple.com/us/app/serialtools/id611021963?mt=12) and [screen](https://en.wikipedia.org/wiki/GNU_Screen)
    * **Linux** - [screen](https://en.wikipedia.org/wiki/GNU_Screen)
4. Follow the instructions printed to the serial monitor. You may have to press CTRL-C and CTRL-D to reset if you don't see anything.
    * IR sensor readings should be around 30,000-60,000 without a surface in front of them and under 5,000 with your hand right in front of them.
    * Encoders should be \~217 ticks per revolution.

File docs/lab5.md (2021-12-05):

# Lab 5: Intro to PID

## Background

You may have noticed that if you let your mouse drive forward for long enough, it'll start drifting to one side. That's because we're just using open-loop control where we apply some input and hope we get the desired output. For various reasons, including but not limited to the following, our mouse will not drive straight even given the same power to both motors.

* The mouse isn't perfectly balanced as all things should be.
* The ground is not perfectly flat.
* Our motors aren't exactly the same.

To fix this, we'll apply something called closed-loop control. Also known as feedback control, we take measurements from the encoders to adjust the power to our motors and drive straight. For example, if we are veering to the left based on encoder readings, we can increase power to the left motor and decrease power to the right motor to correct it.

One common way to do feedback control is PID. For now, you'll be implementing just the P part of it. Conceptually, feedback controllers try to minimize some error which is the difference between a measured value (aka process variable) and setpoint.

For a P controller, we vary our motor power proportionally to our error. That is, the larger our error, the more power we apply to correct for it.

<p align="center">
    
</p>

## Drive Straight

Copy over the skeleton code in [labs/lab5/](../labs/lab5) onto your mouse. Our code is getting too long to just copy paste every time. By default, the code makes the mouse drive forward at 20% speed. Next, copy over your code from [Lab 4](lab4.md) to compute `dist` and `theta` based on encoder readings.

Your job is to apply P control to make the mouse drive straight. The linear velocity doesn't matter too much, just the fact that it doesn't veer left or right. To do this, it would help to answer the following questions.

* What is  when driving straight?
* What is the error when driving straight?
* Given an error, how do you change each motor's power to correct for it?

When implementing the P controller, start with  values of around 0.1 and tune up and down from there based on performance. To make sure the mouse does move forward, add 0.2 to the `throttle` for each motor in addition to your correction term.

### Checkoff #1

1. Demonstrate your working P controller. Print out your error term too.
2. How do you compute the error term?
3. If we want our applied correction power  to be maximized () when the error is 2 radians, what is ?
4. What happens when  is too low? How about too high? What value did you end up using?

## Go the Distance

When solving mazes, it is quite useful to be able to drive forward a set distance. Let's swap out the 0.2 we blindly added to the `throttle` for a linear correction term. Your job is to get your mouse to drive straight forward 200mm and then stop. Like with driving straight, it'd help to answer the following questions.

* What is the error for traveling a set distance?
* Given an error, how do you change each motor's power to correct for it?

When implementing the P controller, start with  values of 0.1 and tune. Don't remove your angular correction code from before since we still want to drive straight. Since we want to leave a little wiggle room for the angular correction, limit the linear correction term to around 0.9.

### Checkoff #2

1. Demonstrate your working P controller. Print out your error term too.
2. How do you compute the error term?
3. If we want our applied correction power  to be maximized () when the error is 100mm, what is ?

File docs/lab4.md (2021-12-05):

# Lab 4: Odometry and Motor Control

## Background

### Odometry

Now that we know how to read the encoders on our mouse, we can use that to estimate the position and orientation of our mouse at any given time. This is a form of *odometry*.

Why is odometry important? Suppose we want our mouse to move forward by one maze cell. We could turn on both motors for a fixed amount of time, and hope the mouse moves exactly the distance we want it to. In practice, this doesn’t work due to friction, changing battery voltage, and many other factors. The difference between the desired movement and the actual movement is called *error*, and knowing the error is the first step towards correcting it.

Using the measurements from both wheels, we can compute the odometry for the entire mouse. Our mouse is a *differential drive* robot, which means that it has two drive wheels located side by side. Both wheels turning in the same direction causes forward (or backward) motion, and both wheels turning in opposite directions causes rotation.

When we describe the position and velocity of a robot, we are actually describing the position and velocity of a single point somewhere on the robot. For a differential drive robot like our mouse, this point is usually taken to be halfway between the wheels. Since a point can’t have a rotational velocity, the “point” is actually a *coordinate frame*. You can think of a coordinate frame as a set of coordinate axes that are “attached” to the mouse and move/rotate with it.

<p align="center">
    
</p>

Consider the coordinate frame in the diagram above. When the mouse moves forward, it moves in the positive x direction. When the mouse rotates, it rotates around the z axis (which points upwards). The concept of coordinate frames is fundamental to robotics, but we won’t be able to cover it in much depth (try EECS C106A if you're interested in this type of stuff!). Fortunately, we only need to know some basics.

<p align="center">
    
</p>

We are mostly interested in the forward distance and rotational distance of our mouse. Intuitively, the center of the mouse moves with a distance that is the average of the wheel distances. Rotation in radians is arc distance divided by diameter which in our case would be the difference in wheel distances divided by the distance between the wheels. We can derive the following formulas.

<p align="center">
    
    <br>
    
</p>

### Motor Control

To make the mouse move, we use brushed DC motors. Applying a voltage across them makes the motor spin in one direction. Reversing this voltage makes the motor spin in the other direction.

Motors need large amounts of current and as such our Pi Pico can't drive them directly from its IO like we could with the LEDs. To solve this problem, we use the DRV8833 motor driver chip. It can drive two small motors and includes features like overcurrent protection and PWM control.

<p align="center">
    
</p>

Above is the DRV8833 breakout board we use in our mouse. One of the motors is connected to the OUT1 and OUT2 pins while the other is connected to the OUT3 and OUT4 pins. The Pi Pico is connected to the INx pins to allow it to control the corresponding OUTx pins.

Since the DRV8833 is a high power device, it needs to be powered off the 9V lithium battery included with your mouse. When using the motors, turn on the switch on your mouse to connect the battery.

To control the motors, we can reference the [datasheet](https://www.ti.com/lit/ds/symlink/drv8833.pdf). The relevant section is copied below for convenience.

<p align="center">
    
</p>

`1` means setting a pin to `True` while `0` means setting it to `False`. `Z` means the pin is "disconnected" which is also known as high impedance mode. Since we power the DRV8833 with 9V, `H` means 9V and `L` means 0V.

## Odometry

Translate the odometry equations into code by filling in the TODOs in the below code. Note that you'll first have to convert the number of encoder ticks to the actual distance traveled.

```python
import board
import time
import rotaryio
from math import pi

lenc = rotaryio.IncrementalEncoder(board.GP12, board.GP13)
renc = rotaryio.IncrementalEncoder(board.GP19, board.GP18)

ENCODER_TICKS_PER_REVOLUTION = """TODO from previous lab"""
WHEELBASE_DIAMETER = """TODO measure this in mm"""
WHEEL_DIAMETER = 34.0 # mm

while True:
    left_dist  = """TODO"""
    right_dist = """TODO"""

    dist  = """TODO"""
    theta = """TODO"""

    print(dist, theta)
    time.sleep(0.05)

```

### Checkoff #1

1. Demonstrate your working code.
2. How many millimeters does a wheel travel per encoder tick?

## Motor Control

Based on the table from the datasheet, the DRV8833 can easily put motors in forward or reverse at full power and even stop. What if we want to use a different speed? To do this we can switch between full power and stop really quickly so that we average out somewhere in between based on the proportion of time we spend in each. This is the main idea behind PWM (Pulse Width Modulation).

CircuitPython has a builtin module for this called `pwmio`. Documentation for it can be located [here](https://circuitpython.readthedocs.io/en/latest/shared-bindings/pwmio/index.html). The important values in PWM are duty cycle and frequency. Duty cycle determines the percentage of time within a cycle spent on. In the case of `pwmio`, it's a 16-bit number (0-65535). Frequency is determined by the total of the on and off times and is specified in Hertz. Since frequency determines the noise, we'll keep it at 20kHz to be at the edge of human hearing.

Look at the `pwmio` documentation and fill in the TODOs below. A duty cycle of 0 or 65535 will set a pin to be completely off or on, respectively. For reasons best explained in a nice [article](https://learn.adafruit.com/improve-brushed-dc-motor-performance/choosing-decay-mode-and-pwm-frequency), we want to switch between the forward and slow decay states of the DRV8833 for PWM.

```python
import board
import pwmio

lmot_in1 = """TODO create PWMOut object on pin GP16 at 20kHz"""
lmot_in2 = """TODO create PWMOut object on pin GP17 at 20kHz"""

while True:
    lmot_in1.duty_cycle = """TODO set to 25% speed forward"""
    lmot_in2.duty_cycle = """TODO set to 25% speed forward"""
```

### Checkoff #2

1. Demonstrate your left wheel spinning forward at 25% speed.
2. What happens if we swap the two PWM pins?

## Motor Control w/ Library

Having to deal with PWM outputs and duty cycles can get tedious. As is usually the case, CircuitPython provides a nice library named `motor` for this very thing. Read the [documentation](https://circuitpython.readthedocs.io/projects/motor/en/latest/api.html) and fill out the TODOs in the following code.

```python
import board
import time
import pwmio
import adafruit_motor.motor as motor

"""TODO don't forget to make PWMOut objects first"""

lmot = """TODO create DCMotor object on pins GP16 and GP17"""
rmot = """TODO create DCMotor object on pins GP15 and GP14""" 

"""TODO set lmot and rmot to SLOW_DECAY"""

while True:
    """TODO move full speed forward for 1s"""

    """TODO brake for 1s"""

    """TODO move 25% speed backward for 1s"""

    """TODO brake for 1s"""
```

### Checkoff #3

1. Demonstrate your code is working.
2. What happens if we pass a `throttle` value larger than 1.0 or -1.0?

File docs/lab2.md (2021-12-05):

# Lab 2: Encoders

## Background

When we're navigating the maze, we'd like to keep track of a couple things.

* Is it driving straight?
* How far has it driven?
* What direction is it facing?

To answer these questions, we'll use the **quadrature encoder** sensors mounted on the back of your motors. They consist of a spinning magnet and two Hall effect sensors mounted 90° apart. Hall effect sensors measure the presence of magnetic fields. In our case, they output a `True` when closer to a north pole and `False` when closer to a south pole.

<p align="center">
    
    <br>
    <a><b>Hall sensor signal (y-axis) vs. time (x-axis)</b></a>
</p>

## Waveform Viewing

Let's try reading raw values from the encoder. Upload the following code.

```python
import board
import time
import digitalio

# left encoder
a = digitalio.DigitalInOut(board.GP12)
b = digitalio.DigitalInOut(board.GP13)

while True:
    print(int(a.value), int(b.value))
    time.sleep(0.001)
```

Pull up a serial monitor and start spinning the left motor at various speeds. Notice how the values start changing. Can you tell which direction the motor is spinning with just one input?

### Checkoff #1

1. What's the output when the motor is stationary? Is it a certain level? Is it constant?
2. How does the output change when you spin the motor faster?
3. Why do we need two Hall effect sensors per motor?

## Polling

Next let's try tracking the position of the left wheel. We're going to use a technique called polling which involves repeatedly reading a signal to detect changes. Fill in the `leftEncoderRisingEdge` function below.

```python
import board
import digitalio

# left encoder
a = digitalio.DigitalInOut(board.GP12)
b = digitalio.DigitalInOut(board.GP13)

counter = 0
position = 0
a_prev = a.value

def leftEncoderRisingEdge():
    global position # access global position
    """TODO increment or decrement position"""

while True:
    a_val = a.value
    if a_val and not a_prev: # rising edge
        leftEncoderRisingEdge()
    a_prev = a_val

    if counter % 1000 == 0:
        print(position)
    counter += 1
```

After uploading the code, pull up a serial monitor and start spinning the motor in both directions. The position should go up and down as you do it!

### Checkoff #2

1. Show your working code.
2. Roughly how many "ticks" correspond to a revolution? How do you think this is computed?
3. What issues might the "polling" method have?
4. Now that we can measure position, how might we measure velocity?
5. What effect does swapping the A and B pins have on how we measure position?

## Interrupts

Polling can be inefficient and even miss edges if the wheel is spinning too quickly. Moreover, constantly having to check a signal takes up a lot of CPU time that could be used for other purposes. While polling is adequate in some cases, for an encoder we need something better.

Interrupts literally interrupt the CPU by making it pause its current task and run some other code before resuming. In our case, we want to trigger an interrupt when a pin has a rising edge. The low-level setup for interrupts usually involves enabling some registers and assigning a function to run. CircuitPython actually abstracts all of this away for us in the `rotaryio` module.

Upload the following code.

```python
import board
import time
import rotaryio

enc = rotaryio.IncrementalEncoder(board.GP12, board.GP13)

while True:
    print(enc.position)
    time.sleep(0.001)
```

Pull up a serial monitor and start spinning the motor.

### Checkoff #3

1. Demonstrate the working code.
2. Why might we use interrupts over polling?

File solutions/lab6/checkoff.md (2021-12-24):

# Lab 6 Checkoff Solutions

## Checkoff #1

1. Remember Riemann sums from calculus? Basically we just add up the measured error over time. Technically we're supposed to multiply by dt, but that's just a scalar error.
2. Go back to the definition of derivative. Basically we take the difference between our current error and previous error. Technically we're supposed to divide by dt, but that again a scalar error.
3. The main idea is that we limit the size of the integral term. A good limit is whatever value of the integral term causes the maximum power to be put into the motor.

## Checkoff #2

1. As long as it drives straight 200mm and stops like in Lab 5, it's good.
2. As long as it turns in place about 90° and stops, it's good.
3. As long as it turns in place about 90° and stops for one second and keeps doing that, it's good. Solution code is in [chk2_code.py](chk2_code.py).
4. They should mention some concept of adding up an error over time. Addressing integral windup by constraining the summation's value is highly recommended, but not necessary.

## Checkoff #3

1. Make sure that the mouse maintains roughly a constant distance from the wall and drives parallel. It should move forward 180mm and stop every second. Solution code is in [chk3_code.py](chk3_code.py).
2. Swap the fixed distance with the right sensor's reading. There are some extra considerations since the angle from both walls are not independent but that's the main idea.

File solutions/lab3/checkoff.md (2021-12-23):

# Lab 3 Checkoff Solutions

## Checkoff #1

1. Just looking to see if the readings are good and consistent with other mice. If not, they might have trouble later.

```python
import board
import time
import digitalio
from analogio import AnalogIn

l_en  = digitalio.DigitalInOut(board.GP7)
l_en.direction = digitalio.Direction.OUTPUT
l_en.value = False
l_adc = AnalogIn(board.GP28)

l_a   = digitalio.DigitalInOut(board.GP5)
l_a.direction  = digitalio.Direction.OUTPUT
l_a.drive_mode = digitalio.DriveMode.OPEN_DRAIN
l_a.value = True # high Z mode

l_b   = digitalio.DigitalInOut(board.GP6)
l_b.direction  = digitalio.Direction.OUTPUT
l_b.drive_mode = digitalio.DriveMode.OPEN_DRAIN
l_b.value = True # high Z mode

while True:
    l_en.value = True

    l_a.value = False
    time.sleep(0.001)
    print(l_adc.value, end=" ")
    l_a.value = True

    l_b.value = False
    time.sleep(0.001)
    print(l_adc.value)
    l_b.value = True

    l_en.value = False

    time.sleep(0.05)
```

## Checkoff #2

1. Like checkoff #1, don't really care about how well they did but instead how they acquired wealth.

```python
import board
import time

from irsensor import IRSensors

ir = IRSensors(
    board.GP7,  board.GP5,  board.GP6,  board.GP28, # left
    board.GP9,  board.GP10, board.GP11, board.GP26, # center
    board.GP21, board.GP20, board.GP22, board.GP27  # right
)

while True:
    ir.scan()
    print("lir_a:", ir.lir_a, "\t", "lir_b:", ir.lir_b, "\t",
            "cir_a:", ir.cir_a, "\t", "cir_b:", ir.cir_b, "\t",
            "rir_a:", ir.rir_a, "\t", "rir_b:", ir.rir_b)
    time.sleep(0.05)
```

## Checkoff #3

1. Just check that they ran the code and have reasonable looking constants. The slope tends to be the same with a slight difference in offset. Around `a=0.03` and `b=-50` appear to be the average.
2. This involves combining taking the sensor readings from the previous checkpoint and implementing the provided equation. Example solution is in [chk3_code.py](chk3_code.py).

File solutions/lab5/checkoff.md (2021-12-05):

# Lab 5 Checkoff Solutions

## Checkoff #1

1. See that the mouse drives straight. Our motors are actually pretty consistent so the difference may not be obvious. The angular error doesn't actually need to go to 0 since we're measuring distance not velocity. It just needs to be stable. Also take a look at their code since this is the first time there's a decent amount of it. Try to encourage them towards clean and readable code. Solution code is in [chk1_code.py](chk1_code.py).
2. Some combination of a target theta minus the actual theta. They could just say theta, but make sure say we can generalize to any desired theta.
3. 
4. Too low and it corrects too slowly or not at all. Too high and it might oscillate and go unstable.

## Checkoff #2

1. See that the mouse drives straight and stops after around 20cm. Don't worry too much about extreme precision. Solution code is in [chk2_code.py](chk2_code.py).
2. Some combination of a target distance minus the current distance.
3.

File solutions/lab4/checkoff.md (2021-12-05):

# Lab 4 Checkoff Solutions

## Checkoff #1

1. Have them manually move the mouse straight and see if the distance roughly matches. Then have them rotate in place and see if the angle matches.

```python
import board
import time
import rotaryio
from math import pi

lenc = rotaryio.IncrementalEncoder(board.GP12, board.GP13)
renc = rotaryio.IncrementalEncoder(board.GP19, board.GP18)

ENCODER_TICKS_PER_REVOLUTION = 217
WHEELBASE_DIAMETER = 78.0 # mm
WHEEL_DIAMETER = 34.0 # mm

while True:
    MM_PER_TICK = pi * WHEEL_DIAMETER / ENCODER_TICKS_PER_REVOLUTION
    left_dist  = lenc.position * MM_PER_TICK
    right_dist = renc.position * MM_PER_TICK

    dist  = (left_dist + right_dist) / 2
    theta = (right_dist - left_dist) / WHEELBASE_DIAMETER

    print(dist, theta)
    time.sleep(0.05)
```

2. About 0.5mm

## Checkoff #2

1. Just needs to be moving at somewhat low speed. Run the code below to get a feel for it. Don't worry about direction. The biggest gotcha is that the IN2 pin needs to be on 75% of the time instead of 25% to get 25% speed.

```python
import board
import pwmio

lmot_in1 = pwmio.PWMOut(board.GP16, frequency=20000)
lmot_in2 = pwmio.PWMOut(board.GP17, frequency=20000)

while True:
    lmot_in1.duty_cycle = 65535
    lmot_in2.duty_cycle = 49151
```

2. Motor direction will reverse.

## Checkoff #3

1. Make sure it does motions specified in the TODOs.

```python
import board
import time
import pwmio
import adafruit_motor.motor as motor

lmot = motor.DCMotor(
    pwmio.PWMOut(board.GP16, frequency=20000),
    pwmio.PWMOut(board.GP17, frequency=20000)
)
rmot = motor.DCMotor(
    pwmio.PWMOut(board.GP15, frequency=20000),
    pwmio.PWMOut(board.GP14, frequency=20000)
)
lmot.decay_mode = motor.SLOW_DECAY
rmot.decay_mode = motor.SLOW_DECAY

while True:
    lmot.throttle, rmot.throttle = 1, 1
    time.sleep(1)
    lmot.throttle, rmot.throttle = 0, 0
    time.sleep(1)
    lmot.throttle, rmot.throttle = -0.25, -0.25
    time.sleep(1)
    lmot.throttle, rmot.throttle = 0, 0
    time.sleep(1)
```

2. It throws an error. Let them know that means we need to keep values within the valid range for future labs.

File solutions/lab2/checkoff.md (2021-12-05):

# Lab 2 Checkoff Solutions

## Checkoff #1

1. Values are constant.
2. It toggles between 0 and 1 faster.
3. To tell direction. Waveform looks the same forward and backward with just one.

## Checkoff #2

1. There's a couple of ways to do it, but here's one.

```python
import board
import digitalio

# left encoder
a = digitalio.DigitalInOut(board.GP12)
b = digitalio.DigitalInOut(board.GP13)

counter = 0
position = 0
a_prev = a.value

def leftEncoderRisingEdge():
    global position # access global position
    position += 1 if b.value else -1

while True:
    a_val = a.value
    if a_val and not a_prev: # rising edge
        leftEncoderRisingEdge()
    a_prev = a_val

    if counter % 1000 == 0:
        print(position)
    counter += 1
```

2. About 217. Multiply the gearbox ratio by the number of north poles on the motor magnet.
3. Basically can miss edges and takes up too much CPU time.
4. Use a timer to measure time between edges.
5. Just reverses the direction of measurement.

## Checkoff #3

1. Does it go up and down.
2. Interrupts don't miss edges and don't need the CPU constantly reading. There's still a limit on speed bc of interrupt and function overhead.

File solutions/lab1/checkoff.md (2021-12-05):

# Lab 1 Checkoff Solutions

## Checkoff #1

1. Not much to say here just make sure the mouse is working.

## Checkoff #2

1. Legit can be any change we just want them to get started tinkering.

## Checkoff #3

1. On for 0.5s and then off for 2s.

## Checkoff #4

1. There's quite a few possible solutions just make sure the RGB LED changes color when the button is pressed. Here's one solution.

```python
import board
import time
import neopixel
import digitalio

rgb = neopixel.NeoPixel(board.GP4, 1)

but = digitalio.DigitalInOut(board.GP3)
but.pull = digitalio.Pull.UP

while True:
    if but.value: # not pressed
        rgb[0] = (0, 69, 69)
    else: # pressed
        rgb[0] = (69, 0, 69)
```

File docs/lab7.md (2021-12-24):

# Lab 7: Maze Solving Primitives (WIP)

The simplest implementation is to just have `forward`, `turn_left`, `turn_right`, and `turn_around` functions. Turning should be pretty easy, but implementing `forward` is trickier as it needs to wall follow, account for lack of walls to reference, and correct for distance errors. Here's some considerations.

- There are 8 possible cases on wall presence for `forward` bc there are 4 walls in consideration when moving forward one cell.
- If we suddenly see an opening on the left or right (or sudden appearance of a wall) we can correct our internal distance measurement.
- We want to maintain 0° with respect to wall on left and right which means an error for each side. If we see openings on the left and right, the errors will point in opposite directions and we should drive straight using just encoders.
- If we start without a wall on one side, we should wall follow using just the other side. May be a concern if that side suddenly lacks a wall so perhaps just drive straight using encoders.
- Should take the minimum of the efforts to correct for both wall angle errors to account for suddenly seeing an opening on one side.

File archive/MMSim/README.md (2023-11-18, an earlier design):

# MMSim

A simulator of the flood fill algorithm for a MicroMouse. It starts by showing the "optimal" Dijkstra's algorithm solution. Then it runs flood fill multiple times between the source and target in the search for the shortest path. There's a bunch of different mazes in the mazes/ folder stored as .txt files. To run one try this:

```
python3 simrh.py mazes/00japan.txt
```

simrh.py simulates a mouse which has sensors on its front, left, and right. simang.py is more like the mouse we use in the DeCal, which has angled sensors and one on the front. To simulate that mouse, use:

```
python3 simang.py mazes/00japan.txt
```

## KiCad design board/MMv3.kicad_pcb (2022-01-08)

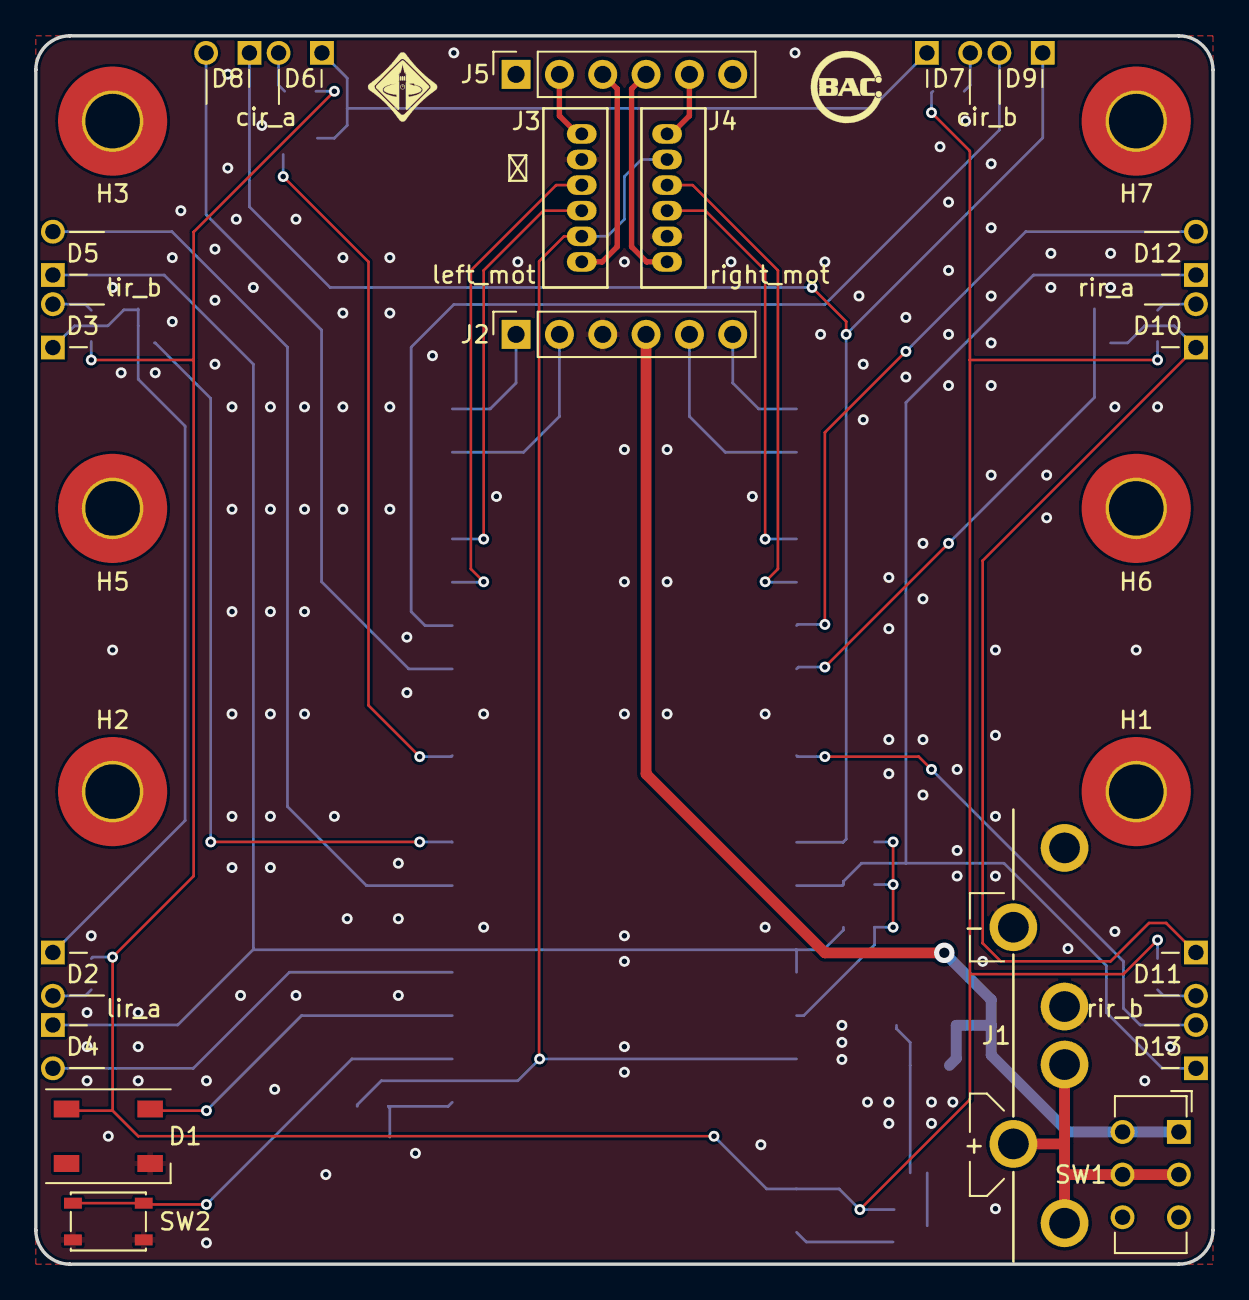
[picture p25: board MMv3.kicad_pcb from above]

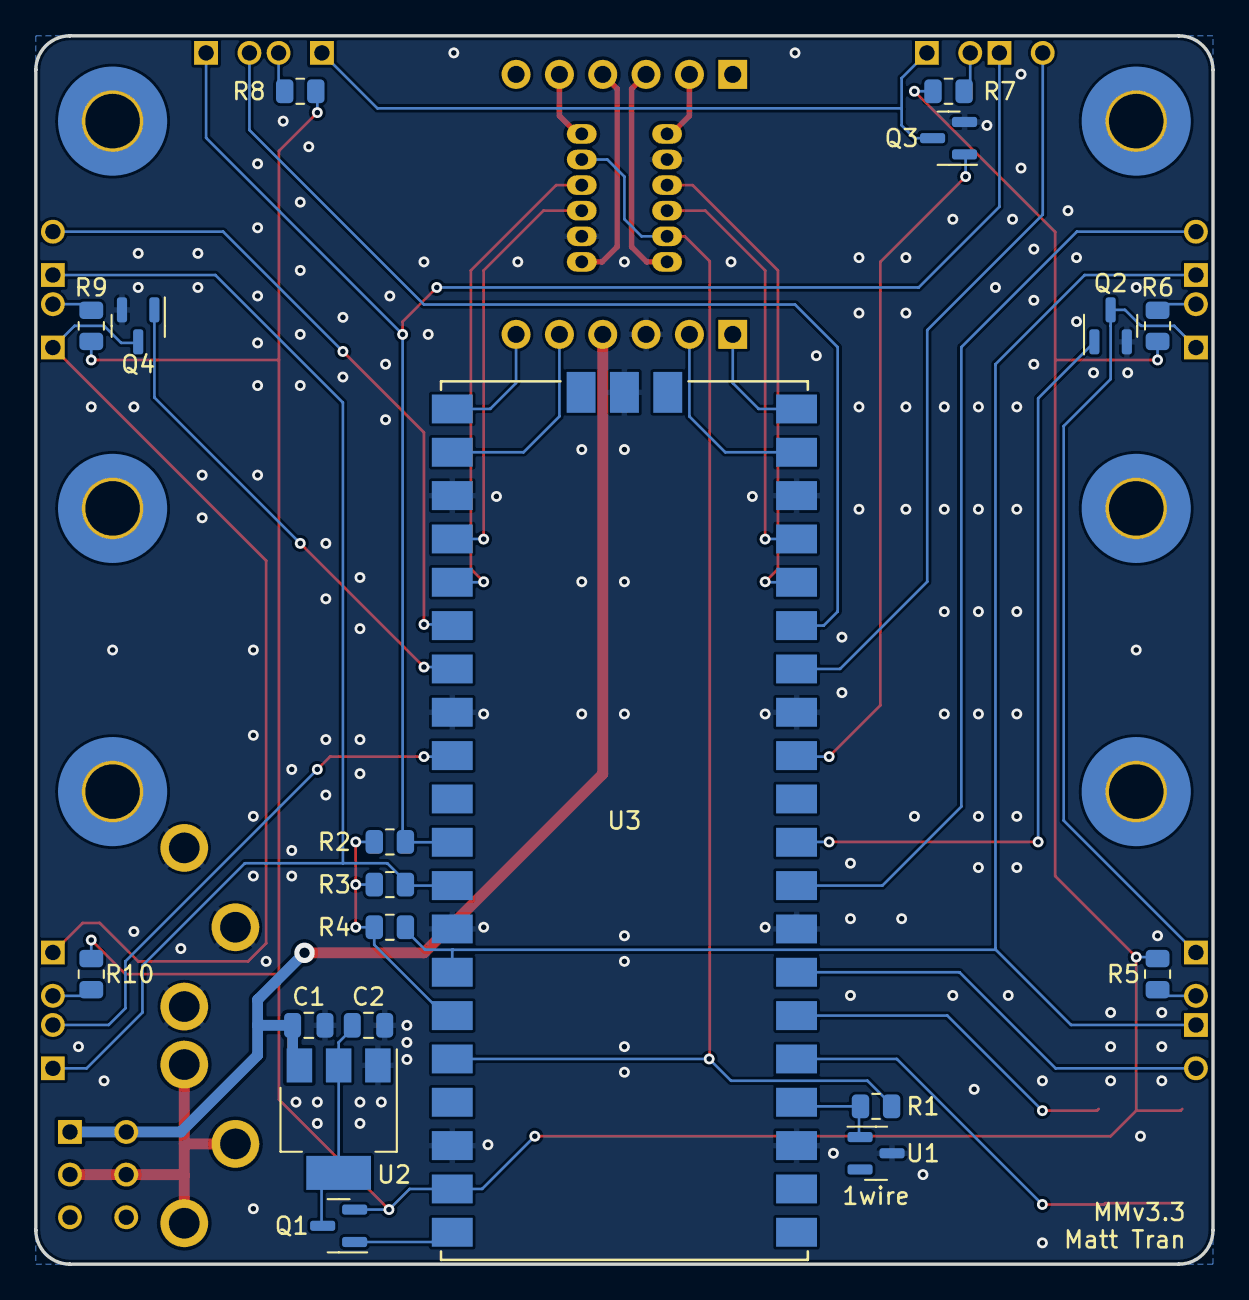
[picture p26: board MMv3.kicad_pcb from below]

Board: 2 copper layers, 69.0 x 72.0 mm, 47 parts (19 on the bottom side), 44 nets.

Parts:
C1, C2: 10u; C_0805_2012Metric
D1: WS2812B; LED_WS2812B_PLCC4_5.0x5.0mm_P3.2mm
D2, D3, D6, D7, D10, D11: LED; LED_D3.0mm_RH_THT_Clear
D4, D5, D8, D9, D12, D13: D_Photo_ALT; LED_D3.0mm_RH_THT_IRBlack
H1, H2, H3, H5, H6, H7: MountingHole; MountingHole_3.2mm_M3_Pad_TopBottom
H4: bac logo; bac_logo
H8: ieee logo; ieee_logo
J1: 9V; Keystone_593_594
J2: DRV8833_L; PinSocket_1x06_P2.54mm_Vertical
J3: left_mot; JST_ZH_Vert_6pin
J4: right_mot; JST_ZH_Vert_6pin
J5: DRV8833_R; PinSocket_1x06_P2.54mm_Vertical
Q1: DMG2301L; SOT-23
Q2, Q3, Q4: DMG2302U; SOT-23
R1: 1k; R_0805_2012Metric
R2, R3, R4: 10K; R_0805_2012Metric
R5, R6, R7, R8, R9, R10: 150; R_0805_2012Metric
SW1: PWR; SW_CuK_JS202011CQN_DPDT_Straight
SW2: but; SW_SPST_PTS810
U1: DS28E05R+T; SOT-23
U2: LD1117S50TR_SOT223; SOT-223-3_TabPin2
U3: RPi_Pico; RPi_Pico_SMD

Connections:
+3V3: J3.5, J4.5, R1.1, U3.36 (3V3)
+5V: D1.1 (VDD), Q1.2 (S), R5.1, R6.1, R7.1, R8.1, R9.1, R10.1, U3.39 (VSYS)
+9V: C1.1, J2.4, SW1.1 (A), SW1.4 (A), U2.3 (VI)
/+3V3A: R2.1, R3.1, R4.1, U3.35 (ADC_VREF)
/but: SW2.1 (A), U3.5 (GP3)
/c_adc: D8.1 (K), D9.1 (K), R2.2, U3.31 (GP26)
/cir_a: D8.2 (A), U3.14 (GP10)
/cir_b: D9.2 (A), U3.15 (GP11)
/cir_en: Q3.1 (G), U3.12 (GP9)
/l_adc: D4.1 (K), D5.1 (K), R4.2, U3.34 (GP28)
/lenc_a: J3.3, U3.16 (GP12)
/lenc_b: J3.4, U3.17 (GP13)
/lir_a: D4.2 (A), U3.7 (GP5)
/lir_b: D5.2 (A), U3.9 (GP6)
/lir_en: Q2.1 (G), U3.10 (GP7)
/lmot_in1: J2.6, U3.21 (GP16)
/lmot_in2: J2.5, U3.22 (GP17)
/lmot_m1: J3.1, J5.2
/lmot_m2: J3.6, J5.3
/neopixel: D1.4 (DIN), U3.6 (GP4)
/onewire: R1.2, U1.1 (DQ), U3.4 (GP2)
/r_adc: D12.1 (K), D13.1 (K), R3.2, U3.32 (GP27)
/renc_a: J4.3, U3.24 (GP18)
/renc_b: J4.4, U3.25 (GP19)
/rir_a: D12.2 (A), U3.26 (GP20)
/rir_b: D13.2 (A), U3.29 (GP22)
/rir_en: Q4.1 (G), U3.27 (GP21)
/rmot_in1: J2.2, U3.19 (GP14)
/rmot_in2: J2.1, U3.20 (GP15)
/rmot_m1: J4.1, J5.4
/rmot_m2: J4.6, J5.5
GND: C1.2, C2.2, D1.3 (VSS), J1.2, J2.3, J3.2, J4.2, Q2.2 (S), Q3.2 (S), Q4.2 (S), SW2.2 (B), U1.3 (GND), U2.1 (GND), U3.3 (GND), U3.8 (GND), U3.13 (GND), U3.18 (GND), U3.23 (GND), U3.28 (GND), U3.33 (GND), U3.38 (GND), U3.D2 (GND)
unnamed: C2.1, Q1.3 (D), U2.2 (VO)
unnamed: D2.1 (K), D3.1 (K), Q2.3 (D)
unnamed: D2.2 (A), R5.2
unnamed: D3.2 (A), R6.2
unnamed: D6.1 (K), D7.1 (K), Q3.3 (D)
unnamed: D6.2 (A), R7.2
unnamed: D7.2 (A), R8.2
unnamed: D10.1 (K), D11.1 (K), Q4.3 (D)
unnamed: D10.2 (A), R9.2
unnamed: D11.2 (A), R10.2
unnamed: J1.1, SW1.2 (B), SW1.5 (B)
VBUS: Q1.1 (G), U3.40 (VBUS)

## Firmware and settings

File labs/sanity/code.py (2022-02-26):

import board
import time

import digitalio
import neopixel
import rotaryio
import pwmio

# from ds28e05  import DS28E05
from irsensor import IRSensors
import adafruit_motor.motor as motor

""" Peripherals """

# debug
led = digitalio.DigitalInOut(board.LED)
led.direction = digitalio.Direction.OUTPUT

but = digitalio.DigitalInOut(board.GP3)
but.pull = digitalio.Pull.UP

rgb = neopixel.NeoPixel(board.GP4, 1)

# extra stuffs
# eeprom = DS28E05(board.GP2)

# IR sensors
ir = IRSensors(
    board.GP7,  board.GP5,  board.GP6,  board.GP28, # left
    board.GP9,  board.GP10, board.GP11, board.GP26, # center
    board.GP21, board.GP20, board.GP22, board.GP27  # right
)

# encoders
lenc = rotaryio.IncrementalEncoder(board.GP12, board.GP13)
renc = rotaryio.IncrementalEncoder(board.GP19, board.GP18)

# motors
lmot = motor.DCMotor(
    pwmio.PWMOut(board.GP16, frequency=20000),
    pwmio.PWMOut(board.GP17, frequency=20000)
)
rmot = motor.DCMotor(
    pwmio.PWMOut(board.GP15, frequency=20000),
    pwmio.PWMOut(board.GP14, frequency=20000)
)
lmot.decay_mode = motor.SLOW_DECAY
rmot.decay_mode = motor.SLOW_DECAY

""" Main """

if __name__ == "__main__":
    # debug
    print("Hello World! Press button to begin tests.")
    while (but.value):
        pass

    print("Blinking the LED underneath your micromouse...")
    for _ in range(6):
        led.value = not led.value
        time.sleep(0.25)

    print("Turning on Neopixel on top of your micromouse...")
    rgb[0] = (255, 0, 0)
    time.sleep(0.5)
    rgb[0] = (0, 255, 0)
    time.sleep(0.5)
    rgb[0] = (0, 0, 255)
    time.sleep(0.5)
    rgb[0] = (1, 1, 1)

    # extra stuffs
    # if eeprom.devices:
    #     print("Detected the following 1-Wire devices...")
    #     for d in eeprom.devices:
    #         print("\t", "".join("{:02x}".format(x) for x in d.rom))

    #     eeprom.write(0, 0, b'MMv3.1')
    #     if not eeprom.read(0, 0, 6) == b'MMv3.1':
    #         print("FAIL! EEPROM write mismatch!")
    # else:
    #     print("FAIL! No 1-Wire devices detected!")

    # IR sensors
    print("Scanning IR sensors! Press button to start and stop.")
    while (but.value):
        pass
    time.sleep(0.05)
    while (not but.value):
        pass

    while (but.value):
        ir.scan()
        print("lir_a:", ir.lir_a, "\t", "lir_b:", ir.lir_b, "\t",
                "cir_a:", ir.cir_a, "\t", "cir_b:", ir.cir_b, "\t",
                "rir_a:", ir.rir_a, "\t", "rir_b:", ir.rir_b
        )
        time.sleep(0.05)
    time.sleep(0.05)
    while (not but.value):
        pass

    # encoders
    print("Reading encoders! Press button to start and stop.")
    while (but.value):
        pass
    time.sleep(0.05)
    while (not but.value):
        pass

    while (but.value):
        print("lenc:", lenc.position, "\t", "renc:", renc.position)
        time.sleep(0.05)
    time.sleep(0.05)
    while (not but.value):
        pass

    # motors
    print("Testing motors! Plug in battery and turn on switch. Press button to start.")
    while (but.value):
        pass

    print("Full speed forward")
    lmot.throttle = 1
    rmot.throttle = 1
    time.sleep(0.5)
    print("Brake")
    lmot.throttle = 0
    rmot.throttle = 0
    time.sleep(0.5)
    print("Full speed backward")
    lmot.throttle = -1
    rmot.throttle = -1
    time.sleep(0.5)
    print("Brake")
    lmot.throttle = 0
    rmot.throttle = 0
    time.sleep(0.5)
    print("Low speed forward")
    lmot.throttle = 0.25
    rmot.throttle = 0.25
    time.sleep(0.5)
    print("Brake")
    lmot.throttle = 0
    rmot.throttle = 0
    time.sleep(0.5)
    print("Low speed backward")
    lmot.throttle = -0.25
    rmot.throttle = -0.25
    time.sleep(0.5)
    print("Brake")
    lmot.throttle = 0
    rmot.throttle = 0
    time.sleep(0.5)

    print("Done with tests!")

    print("Just gonna drive straight now :P")
    while True:
        delta = lenc.position - renc.position
        u = 0.001 * delta
        lmot.throttle = 0.25 - u
        rmot.throttle = 0.25 + u
        print(delta)
        time.sleep(0.05)

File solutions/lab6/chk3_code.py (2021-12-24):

import board
import time
from math import pi

import rotaryio
import pwmio
import adafruit_motor.motor as motor

from irsensor import IRSensors

""" Constants """

ENCODER_TICKS_PER_REVOLUTION = 217
WHEELBASE_DIAMETER = 78.0 # mm
WHEEL_DIAMETER = 34.0 # mm

""" Peripherals """

# IR sensors
ir = IRSensors(
    board.GP7,  board.GP5,  board.GP6,  board.GP28, # left
    board.GP9,  board.GP10, board.GP11, board.GP26, # center
    board.GP21, board.GP20, board.GP22, board.GP27, # right
    avg = 10
)

# encoders
lenc = rotaryio.IncrementalEncoder(board.GP12, board.GP13)
renc = rotaryio.IncrementalEncoder(board.GP19, board.GP18)

# motors
lmot = motor.DCMotor(
    pwmio.PWMOut(board.GP16, frequency=20000),
    pwmio.PWMOut(board.GP17, frequency=20000)
)
rmot = motor.DCMotor(
    pwmio.PWMOut(board.GP15, frequency=20000),
    pwmio.PWMOut(board.GP14, frequency=20000)
)
lmot.decay_mode = motor.SLOW_DECAY
rmot.decay_mode = motor.SLOW_DECAY

""" Extra Code """
class Distance():
    def __init__(self,
        ir,
        la_a, la_b, lb_a, lb_b,
        ca_a, ca_b, cb_a, cb_b,
        ra_a, ra_b, rb_a, rb_b,
    ):
        # store constants
        self.ir = ir
        self.la_a, self.la_b, self.lb_a, self.lb_b = la_a, la_b, lb_a, lb_b
        self.ca_a, self.ca_b, self.cb_a, self.cb_b = ca_a, ca_b, cb_a, cb_b
        self.ra_a, self.ra_b, self.rb_a, self.rb_b = ra_a, ra_b, rb_a, rb_b

        # allocate memory for distances
        self.la, self.lb = 0, 0
        self.ca, self.cb = 0, 0
        self.ra, self.rb = 0, 0

    def scan(self):
        ir.scan()
        self.la = self.la_a * ir.lir_a + self.la_b
        self.lb = self.lb_a * ir.lir_b + self.lb_b
        self.ca = self.ca_a * ir.cir_a + self.ca_b
        self.cb = self.cb_a * ir.cir_b + self.cb_b
        self.ra = self.ra_a * ir.rir_a + self.ra_b
        self.rb = self.rb_a * ir.rir_b + self.rb_b

""" Main """

ir_dist = Distance(ir,
    0.0299, -63.6, 0.0195, -39.1,
    0.0300, -60.4, 0.0251, -47.9,
    0.0258, -50.5, 0.0292, -54.0,
)

def constrain(val, min_val, max_val):
    return min(max_val, max(val, min_val))

# compute dist and theta
def compute_odometry():
    MM_PER_TICK = pi * WHEEL_DIAMETER / ENCODER_TICKS_PER_REVOLUTION

    left_dist  = lenc.position * MM_PER_TICK
    right_dist = renc.position * MM_PER_TICK

    dist  = (left_dist + right_dist) / 2
    theta = (right_dist - left_dist) / WHEELBASE_DIAMETER

    return dist, theta

# compute correction and error terms for a target theta
def compute_u_ang(dist, dist_target):
    Kp_theta = 0.01
    Kp_ang = 0.01

    e_theta = dist_target - dist

    theta_target = Kp_theta * e_theta
    theta = ir_dist.la - ir_dist.lb

    e_ang = theta_target - theta

    u_ang = Kp_ang * e_ang
    u_ang = constrain(u_ang, -0.3, 0.3)

    return u_ang, e_ang

# compute correction and error terms for a target distance
e_lin_sum, e_lin_prev = 0, 0
def compute_u_lin(dist, dist_target):
    Kp, Ki, Kd = 0.01, 0.0005, 0.005

    global e_lin_sum, e_lin_prev
    e_lin = dist_target - dist

    # update I
    e_lin_sum += e_lin
    e_lin_sum = constrain(e_lin_sum, -100, 100) # windup

    # update D
    e_lin_deriv = e_lin - e_lin_prev
    e_lin_prev  = e_lin

    u_lin= Kp * e_lin + Ki * e_lin_sum + Kd * e_lin_deriv
    u_lin = constrain(u_lin, -0.3, 0.3)
    return u_lin, e_lin

def run_control_loop(dist_target):
    dist, theta = compute_odometry()
    ir_dist.scan()
    u_ang, e_ang = compute_u_ang(ir_dist.la, 45)
    u_lin, e_lin = compute_u_lin(dist, dist_target)
    lmot.throttle = constrain(u_lin - u_ang, -1, 1)
    rmot.throttle = constrain(u_lin + u_ang, -1, 1)
    return e_ang, e_lin

def reset_odometry():
    lenc.position, renc.position = 0, 0

def reset_controls():
    global e_ang_sum, e_ang_prev, e_lin_sum, e_lin_prev
    e_ang_sum, e_ang_prev, e_lin_sum, e_lin_prev = 0, 0, 0, 0

def forward():
    reset_odometry()
    while abs(run_control_loop(180)[1]) > 3:
        time.sleep(0.02)
    reset_controls()
    lmot.throttle, rmot.throttle = 0, 0

if __name__ == "__main__":
    while True:
        forward()
        time.sleep(1)

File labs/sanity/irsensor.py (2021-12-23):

import time
import digitalio
from analogio import AnalogIn

class IRSensors():
    def __init__(self, 
        l_en, l_a, l_b, l_adc,
        c_en, c_a, c_b, c_adc,
        r_en, r_a, r_b, r_adc,
        avg = 5
    ):
        # Setup IR LED enables
        self.l_en = digitalio.DigitalInOut(l_en)
        self.c_en = digitalio.DigitalInOut(c_en)
        self.r_en = digitalio.DigitalInOut(r_en)
        for p in [self.l_en, self.c_en, self.r_en]:
            p.direction = digitalio.Direction.OUTPUT
            p.value = False

        # Setup ADCs
        self.l_adc = AnalogIn(l_adc)
        self.c_adc = AnalogIn(c_adc)
        self.r_adc = AnalogIn(r_adc)

        # Setup differential pair enables
        self.l_a = digitalio.DigitalInOut(l_a)
        self.l_b = digitalio.DigitalInOut(l_b)
        self.c_a = digitalio.DigitalInOut(c_a)
        self.c_b = digitalio.DigitalInOut(c_b)
        self.r_a = digitalio.DigitalInOut(r_a)
        self.r_b = digitalio.DigitalInOut(r_b)
        for p in [self.l_a, self.l_b, self.c_a, 
                    self.c_b, self.r_a, self.r_b]:
            p.direction = digitalio.Direction.OUTPUT
            p.drive_mode = digitalio.DriveMode.OPEN_DRAIN
            p.value = True # High Z mode

        # Preallocate memory for storing values
        self.lir_a, self.lir_b = 0, 0
        self.cir_a, self.cir_b = 0, 0
        self.rir_a, self.rir_b = 0, 0

        self.avg = avg

    def scan(self):
        # Enable IR LEDs
        for p in [self.l_en, self.c_en, self.r_en]:
            p.value = True

        # Reset all values to 0
        self.lir_a, self.lir_b = 0, 0
        self.cir_a, self.cir_b = 0, 0
        self.rir_a, self.rir_b = 0, 0

        # Read 'a' channels
        for p in [self.l_a, self.c_a, self.r_a]:
            p.value = False
        time.sleep(0.001)
        for _ in range(self.avg):
            self.lir_a += self.l_adc.value
            self.cir_a += self.c_adc.value
            self.rir_a += self.r_adc.value
        for p in [self.l_a, self.c_a, self.r_a]:
            p.value = True

        # Read 'b' channels
        for p in [self.l_b, self.c_b, self.r_b]:
            p.value = False
        time.sleep(0.001)
        for _ in range(self.avg):
            self.lir_b += self.l_adc.value
            self.cir_b += self.c_adc.value
            self.rir_b += self.r_adc.value
        for p in [self.l_b, self.c_b, self.r_b]:
            p.value = True

        # Compute averages
        self.lir_a, self.lir_b = self.lir_a / self.avg, self.lir_b / self.avg
        self.cir_a, self.cir_b = self.cir_a / self.avg, self.cir_b / self.avg
        self.rir_a, self.rir_b = self.rir_a / self.avg, self.rir_b / self.avg
        
        # Disable IR LEDs (save power)
        for p in [self.l_en, self.c_en, self.r_en]:
            p.value = False

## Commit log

2021-06-27 created board project
    [MMv3.kicad_pcb, MMv3.sch]
2021-06-28 Finished schematic
    [MMv3.kicad_pcb, MMv3.sch, ir.sch]
2021-06-28 Finished layout
    [MMv3.kicad_pcb, MMv3.sch, ir.sch]
2021-06-28 Fixed SWD pinout
    [MMv3.kicad_pcb, MMv3.sch]
2021-10-12 finished mmv3.1 routing
    [MMv3.kicad_pcb, MMv3.sch, ir.sch]
2021-10-12 finished MMv3.1 layout
    [MMv3.kicad_pcb, MMv3.sch, ir.sch]
2021-11-01 fixed 1wire for circuitpython
2021-12-03 finished MMv3.2
    [MMv3.kicad_pcb, MMv3.sch, ir.sch]
2021-12-13 progress on lab 3
    [MMv3.kicad_pcb, MMv3.sch, ir.sch]
2021-12-31 convert to kicad 6
    [MMv3.kicad_pcb, MMv3.kicad_sch, MMv3.sch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]
2022-01-08 adapt to BAC standard capability
    [MMv3.kicad_pcb, MMv3.kicad_sch, ir.kicad_sch]
